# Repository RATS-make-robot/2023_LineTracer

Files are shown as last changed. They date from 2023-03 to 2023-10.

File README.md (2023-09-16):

# 2023_LineTracer

2023 RATS 신입생 라인트레이서 프로젝트

<div align=center>
    
ezgif-5-28c73c5a9f
</div>

## 라인트레이서 대회
- 라인트레이서 완성 후 라인트레이서 대회에서 트랙 1바퀴 완주하면 준회원에서 정회원으로 승급됩니다.
    - 대회에서 여러 번 도전 가능
    - 최소 1회 완주 성공해야 정회원 승급 가능
- __정회원이 되어야 RATS에서 계속 활동할 수 있습니다.__

## 완성 모습



## Schematic(회로도)
2023_LineTracer_1

## 2022년 대비 변경사항
- 차체

_모터 지지대 강화_


_배터리 위치 이동_


- 회로도

_잘못된 센서 방향 및 저항값 수정_
2023_LineTracer_sensors

## 부품리스트

[부품리스트 (가격과 판매처 링크가 포함된 버전)](https://mokhwasomssi.notion.site/bc81dec099644cce938beb7883b7c5f4)
- 소자
    |부품|종류|용도|비고|
    |---|---|---|---|
    |아두이노 나노 호환보드|MCU|라트 개발보드|  
    |스위치|스위치|라트 전원 스위치|
    |7805|레귤레이터|전원부 레귤레이터|
    |캐패시터 0.33uF|커패시터|전원부 커패시터|
    |캐패시터 0.1uF|커패시터|전원부 커패시터|
    |저항 330Ω|저항|LED 저항|
    |저항 10kΩ|저항|수광 소자용 저항|2022년:1MΩ
    |저항 220Ω|저항|발광 소자용 저항|
    |LED|LED|전원부 출력 확인, 센서 값 확인|
    |KID05BW85|발광 소자|주행선 감지|2022년:ST5811
    |ST5811|수광 소자|주행선 감지|2022년:SI5312-H

- 모터, 배터리
  |부품|종류|용도|
  |---|---|---|
  |아두이노 RC카 모터|모터|모터|
  |아두이노 RC카 바퀴|바퀴|바퀴|
  |배터리 18650 1200mAh|배터리|리튬 이온 배터리, 충전 가능|
  |배터리 홀더|배터리|18650x2 홀더|

- 소켓, 커넥터, 점퍼
  |부품|종류|용도|
  |---|---|---|
  |핀헤더|소켓|12핀 : 센서 전원, 신호  </br> 8핀 : 모터 전원, 신호|
  |핀헤더소켓|소켓|30핀 : 아두이노</br>3핀 : 레귤레이터|
  |몰렉스 커넥터 - M|커넥터|전원 커넥터|
  |몰렉스 커넥터 - F|커넥터|전원 커넥터|
  |소켓 점퍼 케이블 - F/F|점퍼|센서 전원 및 신호</br>모터드라이버 신호|
  |소켓 점퍼 케이블 - M/F|점퍼|모터드라이버 전원</br>모터 전선|

- 조립
  |부품|종류|용도|
  |----|---|---|
  |부품 수납 케이스|공구함|개인 부품 보관|
  |만능기판 100X100|만능기판|메인보드 납땜|
  |만능기판 100X50|만능기판|센서보드 납땜|
  |서포트 40mm|서포트|메인보드 서포트|
  |서포트 10mm|서포트|모터드라이버 서포트|
  |볼트 M3x10|볼트|메인보드 서포트 고정</br>모터드라이버 서포트 고정</br>볼캐스터 고정</br>센서보드 고정|
  |볼트 M3x16|볼트|몸체-몸체2 조립|
  |볼트 M3x30|볼트|모터 고정|
  |너트 M3|너트|너트|
  |볼캐스터 5/8|볼캐스터|앞바퀴|

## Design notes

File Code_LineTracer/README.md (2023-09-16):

### 위 코드를 가지고 아래 트랙을 돌려보며 자신의 로봇에 맞도록 코드의 값을 맞춰주세요.
<div align=center>
  
ezgif-5-28c73c5a9f
</div>

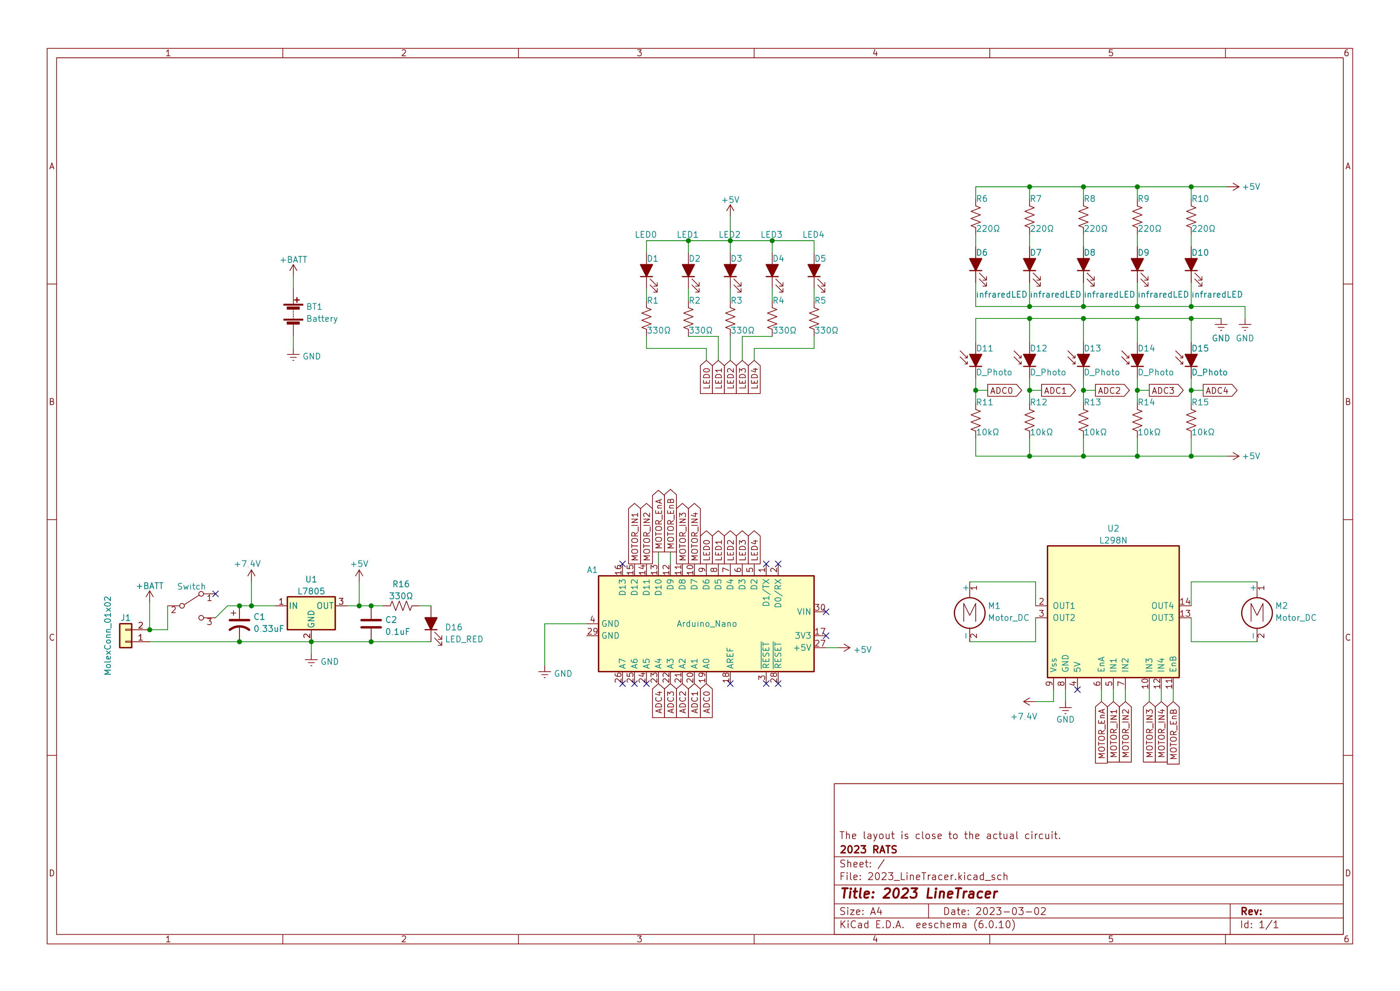
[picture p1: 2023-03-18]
Schematic/2023_LineTracer.png

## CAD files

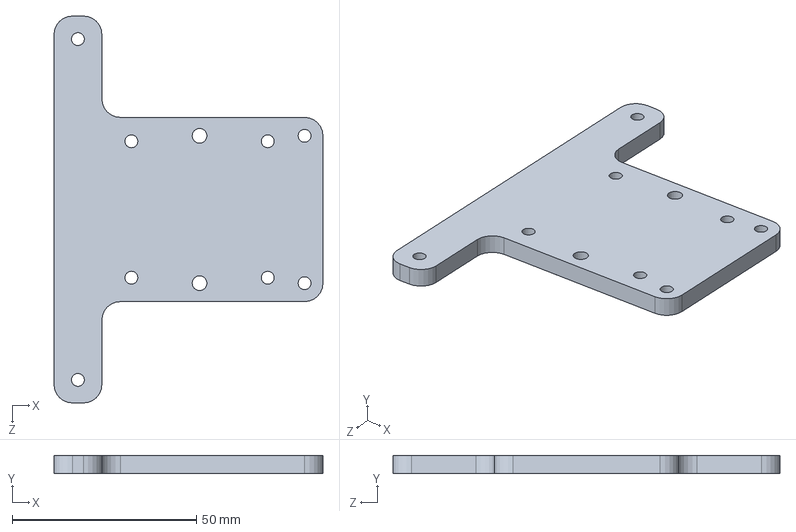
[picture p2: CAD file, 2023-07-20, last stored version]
Modeling/몸체2 2022.SLDPRT
73.0 x 5.00 x 105.0 mm

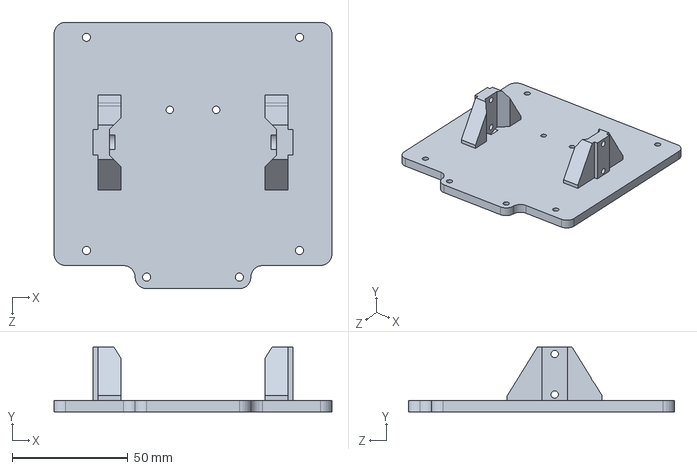
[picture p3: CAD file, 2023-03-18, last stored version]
Modeling/몸체 2023.SLDPRT
120.0 x 28.0 x 115.0 mm

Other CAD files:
Modeling/몸체 2023.STL
Modeling/몸체2 2022.STL

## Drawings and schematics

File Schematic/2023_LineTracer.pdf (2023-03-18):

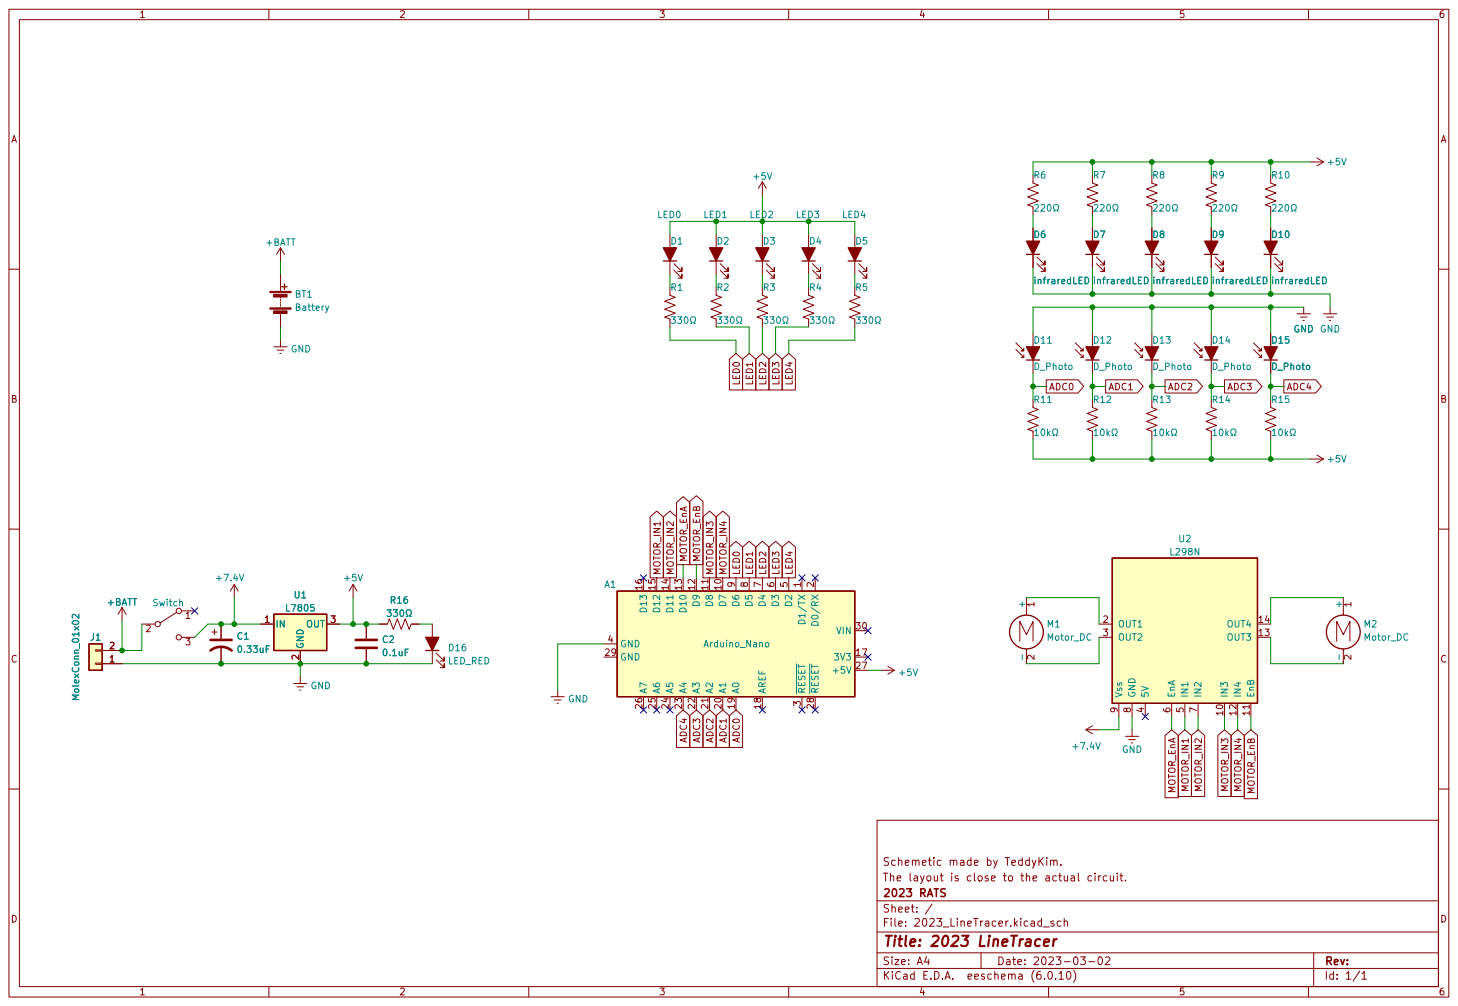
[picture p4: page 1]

2 A1 20 A2 21 A3 22 A4 23 A5 24 A6 25 A7 26 +5V 27 ~{RESET} 28 GND 29 ~{RESET} 3 VIN 30 GND 4 D2

Schemetic made by TeddyKim.
The layout is close to the actual circuit.
File: 2023_LineTracer.kicad_sch Sheet: / 2023 RATS

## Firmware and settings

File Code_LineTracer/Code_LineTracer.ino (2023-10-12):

#define MOTOR_OFFSET_LEFT 100  //본인꺼에 맞게 바꿀 값
#define MOTOR_OFFSET_RIGHT 100 //본인꺼에 맞게 바꿀 값

#define TARGET_LINE 0
#define kP 7  //본인꺼에 맞게 바꿀 값

#define SERIAL //시리얼 통신 안 쓰려면 주석처리하기

const int LED_pin[5] = {6, 5, 4, 3, 2};
const int sensor_pin[5] = {A0, A1, A2, A3, A4};

const int ENA = 9;   //모터 ENABLE A 핀
const int ENB = 10;  //모터 ENABLE B 핀
const int IN1 = 7;   //왼쪽 모터 방향 핀
const int IN2 = 8;
const int IN3 = 11;  //오른쪽 모터 방향 핀
const int IN4 = 12;

int sensor_value[5] = {0}; //센서 값 저장 변수
int sensor_standard[5] = {200, 200, 200, 200, 200}; //센서 기준값 설정 변수(캘리브레이션 사용 X경우)
int line_hex; //라인 위치 정보 저장 변수

void read_sensor(); //센서값 읽어서 "sensor_value"에 저장 후에 -> bit 형식으로 "line_hex"로 저
void monitoring_sensor(); //센서값 정보 -> UART출력 & LED출력 함수
void motor(int left_speed, int right_speed); //왼쪽/오른쪽 모터 속도 설정 함수
int curent_line(); //센서값 정보 -> 현재 라인 위치 판별 함수
void pControl(); //P제어 함수

void setup() {
#ifdef SERIAL
  Serial.begin(9600);
#endif
//아트메가의 모든 핀의 기본값은 입력이기 때문에 불필요 하지만 오류를 대비해 pinMode(SENSOR[i], INPUT) 입력
  for (int i = 0; i < 5; i++) {
    pinMode(sensor_pin[i], INPUT); //모든 센서는 INPUT으로 설정
    pinMode(LED_pin[i], OUTPUT); //모든 LED는 OUTPUT으로 설정
    digitalWrite(LED_pin[i], HIGH); //모든 LED의 초기값은 HIGH로 설정 -> sink 전류로 동작하기 때문
  }
  pinMode(ENA, OUTPUT); //모터 드라이버로 가는 핀들은 모두 OUTPUT
  pinMode(ENB, OUTPUT);
  
  pinMode(IN1, OUTPUT);
  pinMode(IN2, OUTPUT);
  pinMode(IN3, OUTPUT);
  pinMode(IN4, OUTPUT);
}

void loop() {
  read_sensor();//센서값을 읽고
  monitoring_sensor();//센서값을 UART & LED5개로 출력하고
  pControl();//그 센서값(라인 위치)에 따라 모터 속도 제어
}
/*********************************************************/
void read_sensor() {
  for (int i = 0; i < 5; i++) //센서값 읽어서 "sensor_value"에 저장
    sensor_value[i] = analogRead(sensor_pin[i]);

  line_hex = 0; //기준값보다 크면 검정색인 부분
  if( sensor_value[0] > sensor_standard[0] ) 
    line_hex += B10000; //왼쪽에서 0번 센서가 기준값보다 크면 이진수 0b 1 0000를 "line_hex"에 더해줌
  if( sensor_value[1] > sensor_standard[1] ) 
    line_hex += B01000; //왼쪽에서 1번 센서가 기준값보다 크면 이진수 0b 0 1000를 "line_hex"에 더해줌
  if( sensor_value[2] > sensor_standard[2] ) 
    line_hex += B00100; //왼쪽에서 2번 센서가 기준값보다 크면 이진수 0b 0 0100를 "line_hex"에 더해줌
  if( sensor_value[3] > sensor_standard[3] ) 
    line_hex += B00010; //왼쪽에서 3번 센서가 기준값보다 크면 이진수 0b 0 0010를 "line_hex"에 더해줌
  if( sensor_value[4] > sensor_standard[4] ) 
    line_hex += B00001; //왼쪽에서 4번 센서가 기준값보다 크면 이진수 0b 0 0001를 "line_hex"에 더해줌
}// ==> 결과적으로 라인 위치가 5비트로 표현됨

void monitoring_sensor() {
#ifdef SERIAL
  Serial.print(sensor_value[0]); Serial.print("\t"); //센서값 UART 출력
  Serial.print(sensor_value[1]); Serial.print("\t");
  Serial.print(sensor_value[2]); Serial.print("\t");
  Serial.print(sensor_value[3]); Serial.print("\t");
  Serial.print(sensor_value[4]); Serial.print("\t");
  
  if(line_hex <= B1111)Serial.print("0"); //"line_hex"를 출력할 때 높은 자리수가 0일 때 0을 채워주는 부분
  if(line_hex <= B111)Serial.print("0");
  if(line_hex <= B11)Serial.print("0");
  if(line_hex <= B1)Serial.print("0");
  Serial.print(line_hex, BIN);
#endif
  PORTD |= 0x7C; //LED전부 HIGH를 줘서 끄기
  PORTD &=~ line_hex<<2; //인식된 센서 그대로 LED 켜기
} // "<<2"는 PD2부터 LED니까 PD2자리부터 시작하도록 "line_hex"를 2칸 밀어줌

/*********************************************************/
void motor(int left_speed, int right_speed) { //왼쪽/오른쪽 모터 속도 설정 함수
  digitalWrite(IN1, HIGH); //모터 전진
  digitalWrite(IN2, LOW);
  digitalWrite(IN3, HIGH);
  digitalWrite(IN4, LOW);

  analogWrite(ENA, left_speed); //모터 속도 변경
  analogWrite(ENB, right_speed);
}

int curent_line() { //센서 정보(line_hex) -> 현재 라인 위치 판별 함수
  switch(line_hex)
  { //"line_hex"의 1은 검정색을, 0은 흰색 배경을 나타냄 00100이면 라인이 라인트레이서 중앙에 있다는 것
    case B10000: return -4;
    case B11000: return -3;
    
    case B01000: return -2;
    case B01100: return -1; //음수는 라인트레이서 기준으로 라인이 왼쪽에 있다는 것, 숫자 크기는 중앙에서 얼마나 떨어졌는지 나타냄
    
    case B00100: return 0; //0을 중알으로 설정
    
    case B00110: return 1; //양수는 라인트레이서 기준으로 라인이 오른쪽에 있다는 것, 숫자 크기는 중앙에서 얼마나 떨어졌는지 나타냄
    case B00010: return 2;
    
    case B00011: return 3;
    case B00001: return 4;

    case B11110: return 100; //교차점 직진
    case B11111: return 100;
    case B01111: return 100;
  }
}

void pControl() { //P제어 함수
  int current_line = curent_line(); //바로 위에 있는 함수인 "curent_line()"에서 return한 값을 
  if (current_line == 100) current_line = 0;// 교차점일 때는 중앙으로 인식하고 직진하기 { curent_line()에서 return 0;해도 상관 없음 }
  int error = current_line - TARGET_LINE; //얼마나 중앙에서 벗어났는지 "error" 값 계산
  int control_sensor = kP * error;
#ifdef SERIAL
  Serial.print("\t속도차이: "); //두 모터의 속도 차이 출력
  Serial.print(control_sensor);
  Serial.println(" * 2");
#endif
  motor((MOTOR_OFFSET_LEFT - control_sensor),  //왼쪽 모터 속도 조절
        (MOTOR_OFFSET_RIGHT + control_sensor));//오른쪽 모터 속도 조절
}

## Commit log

2023-10-12 주석 추가 #1
2023-10-12 주석 추가 #3
